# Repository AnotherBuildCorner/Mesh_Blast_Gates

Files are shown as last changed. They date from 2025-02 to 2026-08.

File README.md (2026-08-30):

# Mesh_Blast_Gates
## Currently Under Construction

What happens when you combine a Woodworker, and an Electrical Engineer? 
Sometimes the result are things like this. A Mesh controlled set of blast gates for dust collection control.

But first, why did I even bother making this? Cost, and Convenience. Products that can do this already exist on the market. However they cost somewhere around $125 USD PER GATE! Plus additional modules to handle higher power collection 230V systems. Plus I wanted to add advanced features like timers, and a rechargable pocket remote.

On top of that, I already had a fully built system utilizing manually actuated metal blast gates. It really felt like a total waste to rip these gates out in place of some closed solution. And some of the places i wanted to move my existing gates to are inacessible in the course of day to day operation. The commercial option has a switch mounted to the body. Which would impede that solution.

Instead I chose to launch my own system using my pre-existing knowledge of ESP32's and high power hobby servos. 

## Core Architecture.
First things first, the main parts:

The brains of the whole operation. Xiao C6 model ESP 32's. Chosen for their small form factor, while supporing enough GPIO pins to control the system, and supporting a socket mount (A wonderful bit of foresight... More on that later).

Additionally, I wanted a prebuilt serial system for flashing and monitoring, which this provides like many other DEV style boards.

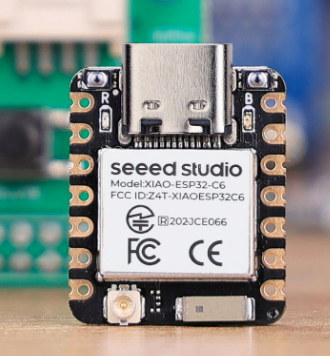
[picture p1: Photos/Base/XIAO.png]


The mechanics driving the actual gates are these servos: 20KG 270 deg servos, Relatively low cost, and when provided enough current/voltage have plenty of torque to do the job.

At right is the actual blast gate for reference.

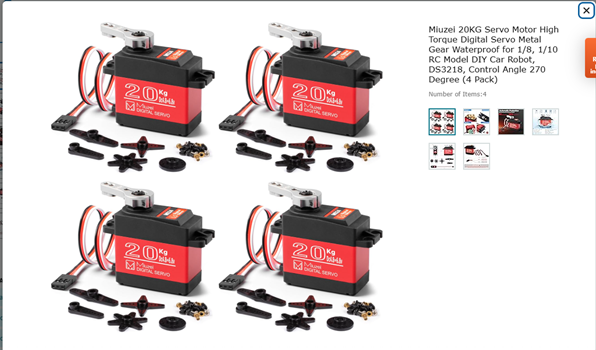
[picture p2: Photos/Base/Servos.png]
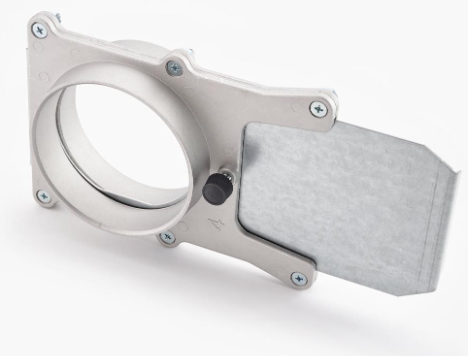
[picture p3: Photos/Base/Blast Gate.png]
  

Interconnect Diagram

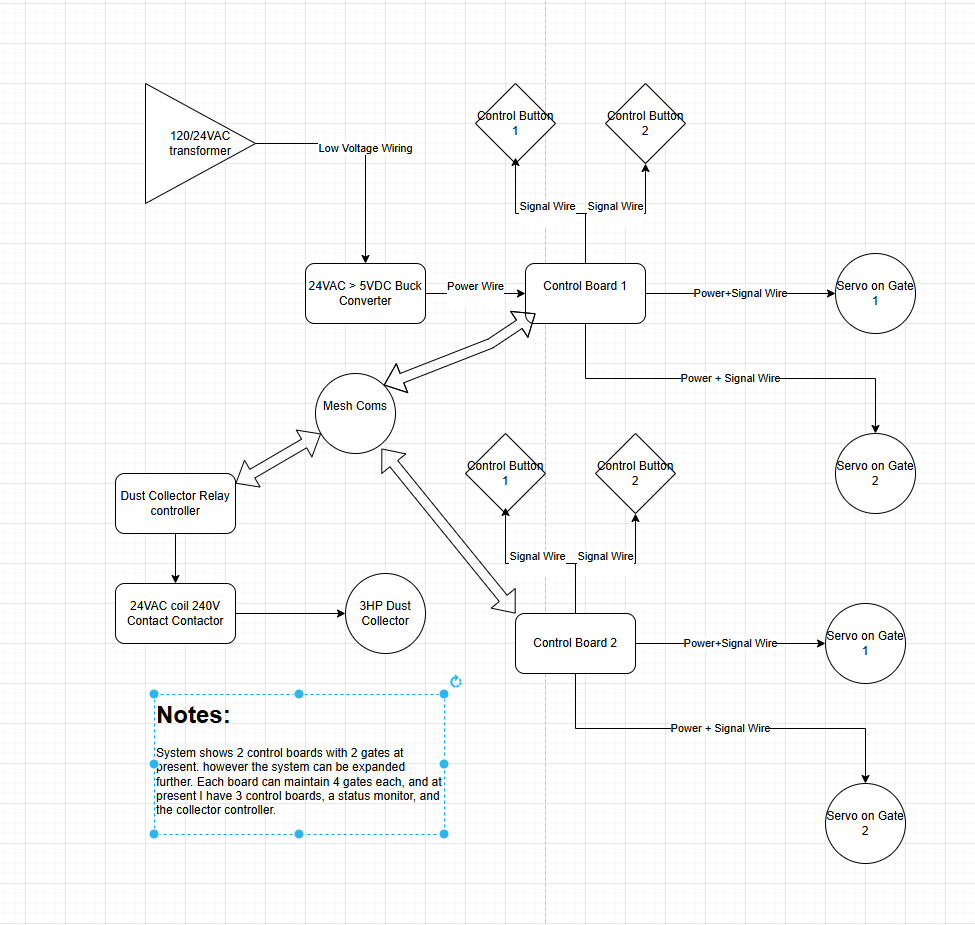
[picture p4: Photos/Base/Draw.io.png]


A rough picture of the pricing
Per Gate
- $20 per metal gate (already had on hand)
- $10 per servo
- $2 for 100G of 3D print Filament
- $2 misc overhead

Per Control Board as of Febuary 2025
- $5 per XIAO C6
- $1 per PCB
- $1 per Buck Boost Chip
- 1$ per Inductor (I used way oversized ones for low frequency switching)
- $5 rough estimate of additional parts (switches and such)
- $10 per USB power brick and cable (Some of us have mountains of these around) 

Per System cost
- $20 per 24V Transformer
- $10 per 204V-24V contactor
- $2 per 5V signal relay (for the collector control board)
- $5 per Xiao C6 for Collector only
- $20 for a roll of 22 gauge silicon wire for switches

So for my system, which uses 8 gates, 3 control boards, and a relay board the total cost comes up to around...
- Per gate costs: $ 280
- Per Board costs $ 69
- Per System costs $ 57
- Total: $ 416
- for my own cost I already had the blast gates and usb cables on hand, so -$ 190

## Notes:
There are some improvements left to be implemented. The core of which is still better power distribution/control. As well as updating the physical gate structures.
things i'd like to add
### PCB
- Completed desired updates. see V3
### Mechanical

- Add some form of mechanical clutch system.
- - Spring or screw compressed V band on the pinion (spring prefered, but introduces complexity and potential calibrations)
- - Switch from rack and pinion to V wheel and slider with TPU surface
- - add a slider into the rack with a helical spring mounted for bi-directional movement
- - Add TPU teeth to the rack or pinion so they can slip under excessive tension

### Code
- Current code has a strict 1HR timer on dust collection before shutdown
- modify to enable longer run times, or change the switch type specifically for the CNC to enable CNC controlled collection.
- maybe add a custom sender board just for the CNC. Not sure I want hard wires to a tool on wheels... (besides power)
- implement multi-gate control from one switch for cases like multiple gates to one tool
- add a multiple tool mode. Say having the CNC active and a drum sander. 
- consider changing the direct peer-peer mesh to a central node structure. Every time I have to replace one chip, reflashing the entire network is required... and some of the chips are hard to reach. Ideally an auto-detect model would be great.

## V3 

### PCB
V3 PCB is now live. Implementing two desired changes over the V2 Board.
The first is integrating the TVS diodes into the PCB on both the Servo signal lines, as well as the input switches. So far this has prevented any fried servos or bad ESP's in testing.
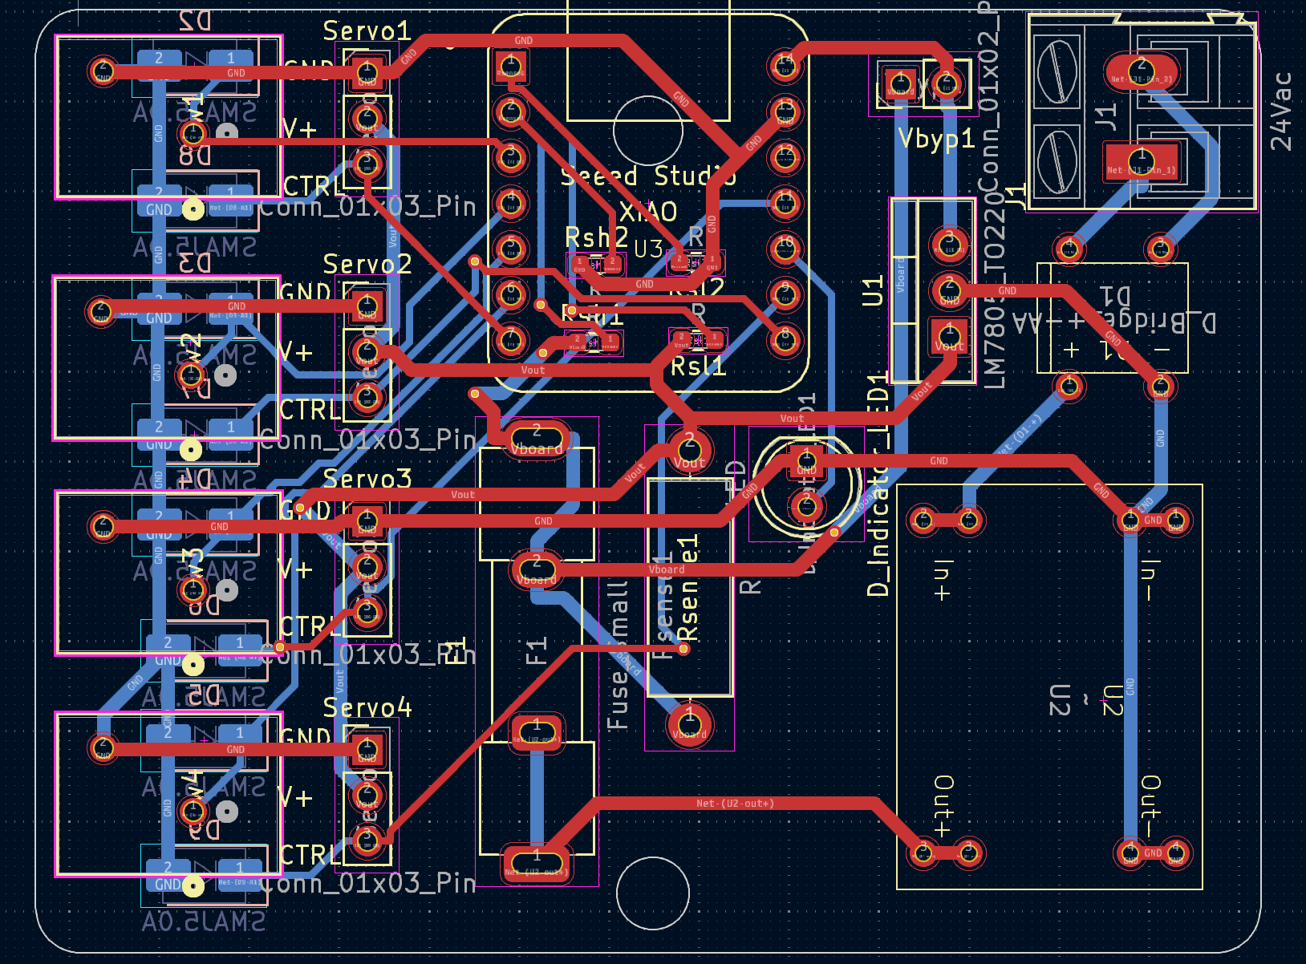
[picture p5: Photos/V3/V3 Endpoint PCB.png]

Second is the Buck-Boost board has been swapped for a commercially available premade PCB. The board provides up to 24V input, and trim controlled output. The PCB also includes a new LED tied directly to the ESP, this LED is programmed to illuminate between 7 and 8V currently to allow calibrating the new board.
The input Bridge Rectifier has been retained, as well as the smoothing cap. This allows for polarity agnotsic DC, as well as AC input for the boards. Currently running on 12V mains.

### Mechanical.
The gear drive system has been slightly refined.
The teeth are now 2mm straight cut gears, with a wider dual guide Rack, and a slot cut into one end to capture the blast gate without additional hardware. The baseplate has been thickened by an additional 2mm. and the gears now feature a multiple cut design on the underside to accomodate multiple servo horn shapes besides the round one. No more skipping of the gears now.
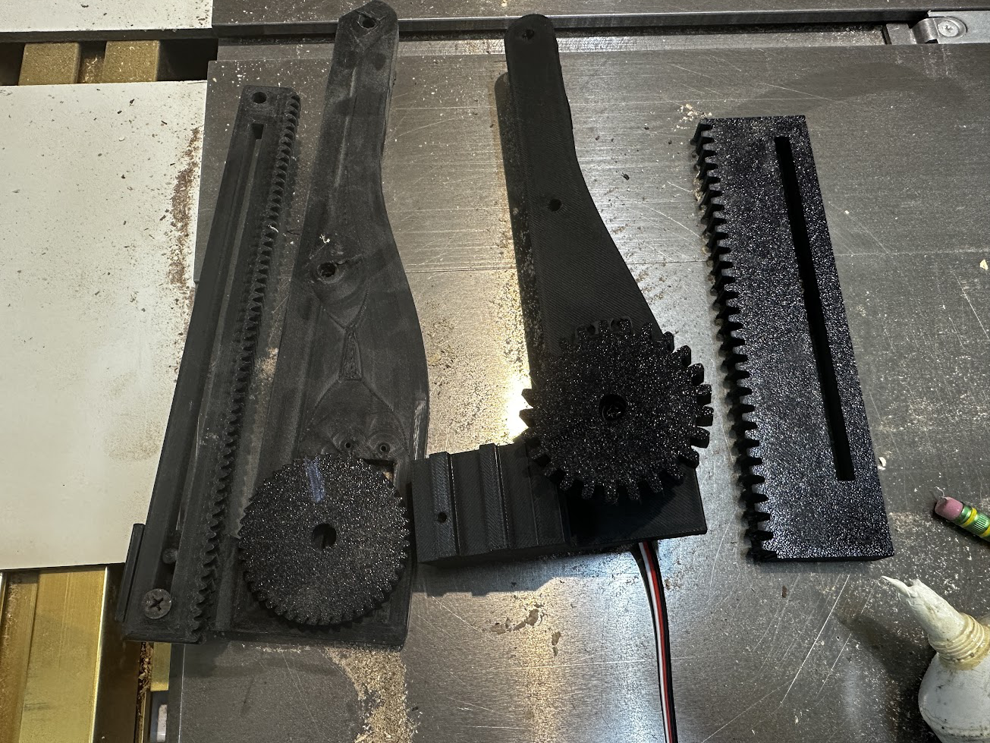
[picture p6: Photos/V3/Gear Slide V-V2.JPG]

### Code
The system now runs on a central node with a display screen. This way anytime the system is updated (say an ESP dies, or a new board is added) only the new board, and the central node need to be reflashed. Instead of correcting the entire system.
a strict 2 hour timer has been implemented for both short and long press gate openings.

Current sensing is back online in dual ended mode. With a 1.5A current limit, which enforces a chip reset currently. Future updates will force the gate to stop in position. No boards fried yet, but a couple fuses tripped due to user error.

Additionally, the central node has a configurable resend timer. In the past messages were failing to shut down the dust collector as required. With this resend, reliability has reached 100%, although sometimes it can take up to 3 cycles.

Future additions will be to include some kind of current sensing, or non-pushbutton operation perhaps. For things like CNC's with vacuum switching relays, or hall-effect sensors on certain tools. 
Also, the dual gate mode may be updated to set both gates to partially open, to retain system pressure.  TBD.
Lastly, it would be ideal to push all the configuration settings from the central node. so only a preliminary flash will be needed for each endpoint.  For now this is a stretch goal.

### Previous IN PROGRESS notes for V3
Well, as one set of errors is removed, a new set begins to rear its ugly head. 

### PCB
At present a new PCB has not been generated. Currently in the troubleshooting phase.
As it stands right now, it appears the system would function on a metal ducted dust collection system, because the entire tubing would have an ESD potential of 0, being grounded somewhere. However, my system is PVC based, as such it collects static charges.

Initially I did not pursue ESD hardening because I did my best to isolate the switch wires from the dust pipe runs, as well as the servos are on isolated plastic brackets, again with minimum wire near the potentially charged pipes.

However this has not been enough. As it seems the ESP32 chips have been bricking at seemingly random times. Although it always seems to be on a chip that had an active flow of air through a connected gate, which was then switched to a different gate. 

To rectify this, I have placed Unidirectional TVS diodes in two places thus far. The first batch went on each of the input switches connected from signal to ground. This alone did not fix the problem, as shortly after implementing, another board fried.
The second batch is connected from each of the servo signal wires to ground. This setup remains to be tested.

Board with TVS Diodes added: Note, the switches are configured in switch to ground with PULL_UP enabled on the XIAO. So the TVS diodes clamp the voltage to 5V which is within acceptable ranges for the XIAO even though it's a 3.3V microcontroller.

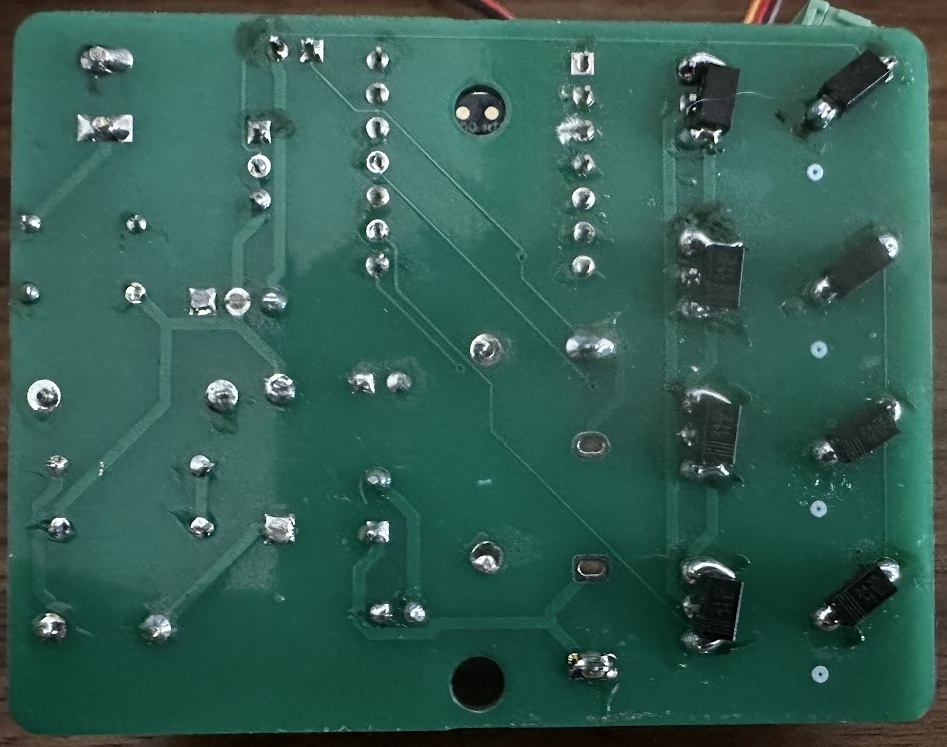
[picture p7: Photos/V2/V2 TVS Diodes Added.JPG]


For now I have switched to powering the system on 5V 1A usb power supplies for each module, as I ran out of the Buck controller chips, and as of right now USB power has proven more than powerful enough to control all but my largest gate with the entire system closed and under vacuum. Additionally I encountered some bad wire that had internal insulation problems which shorted out my transformer.  Sometimes it's best to know when to stick with what's working...  I will likely revisit the Buck controller at a later date. First is solving the frying ESP32's  otherwise this system is a useless brick.

## V2
Version 2 corrects a lot of the mistakes Version 1 made, and has resulted in a functional system, but is still far from complete.

### PCBs 
First, the PCB has been updated to contain power limiting safety measures. Among these are Fuse 1, set to a 1 amp glass tube fuse. and the addition of the large curent sense resistor RSense. Additionally a network of voltage dividers has been added to drop the 5-7 volt voltages at Rsense terminals to the 3.3V the ESP ADC can handle.

The system uses dual ended current sensing, with the resistance of Rsense known to within 1% and programmed. Voltage is measured at each terminal, the difference calculated, and from that current through the resistor is determined. This is used to initiate a restart in the code. As the gates are programmed to not move until a command is sent, this functions as a pause. This is temporary, in time a better response to a binding gate, like bounce or a simple stop will be implemented.

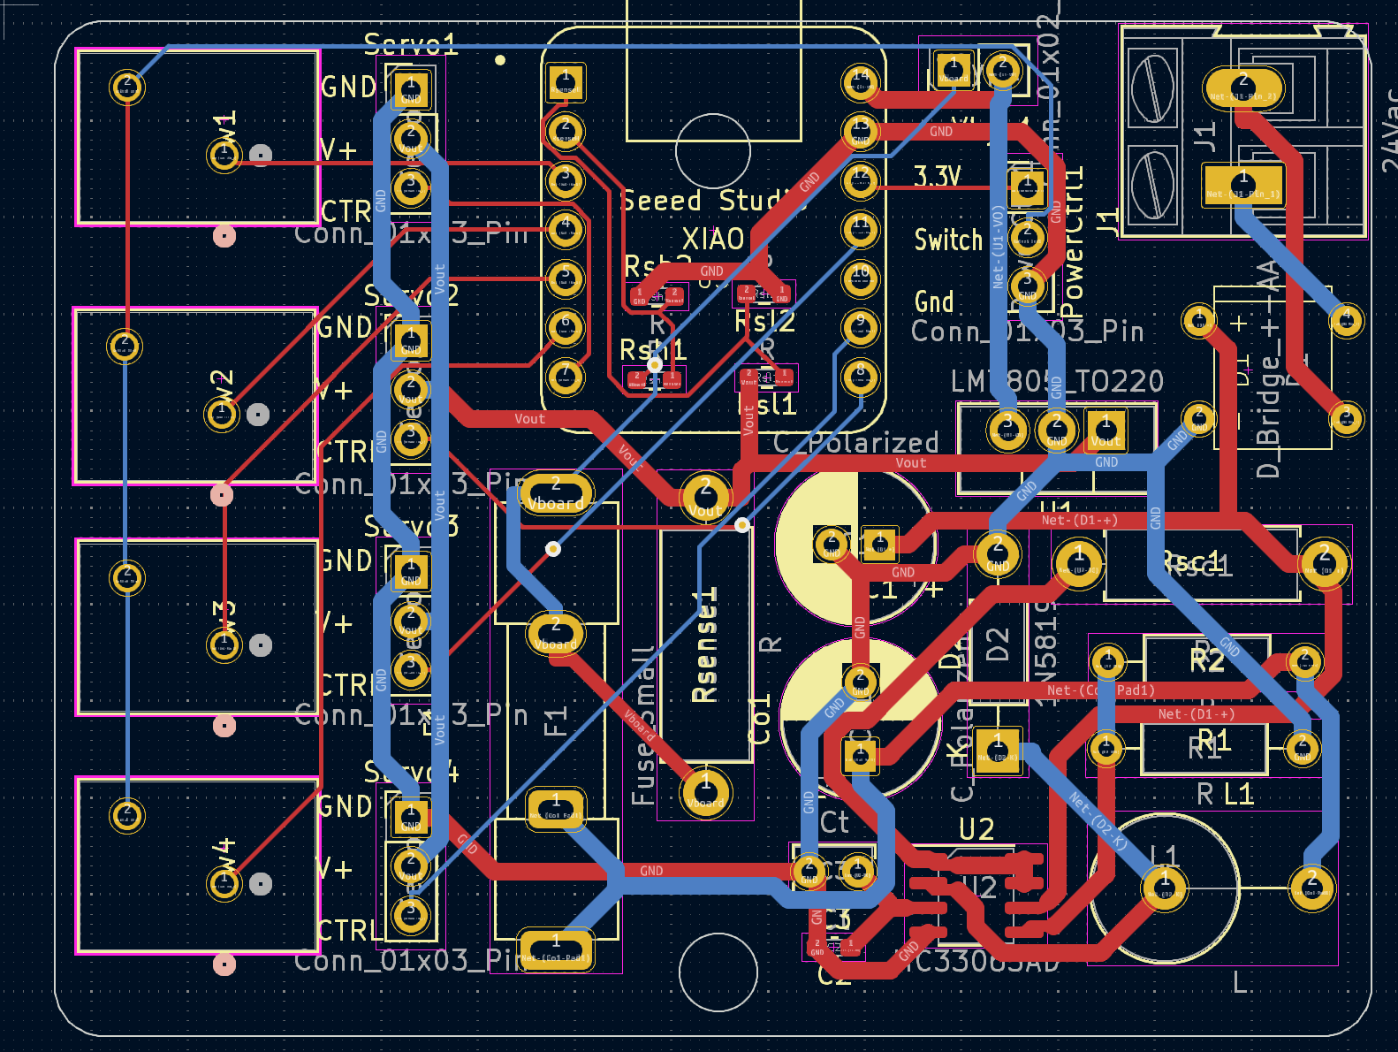
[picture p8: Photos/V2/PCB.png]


Additionally, a second PCB for controlling two possible Dust collection units has been added.

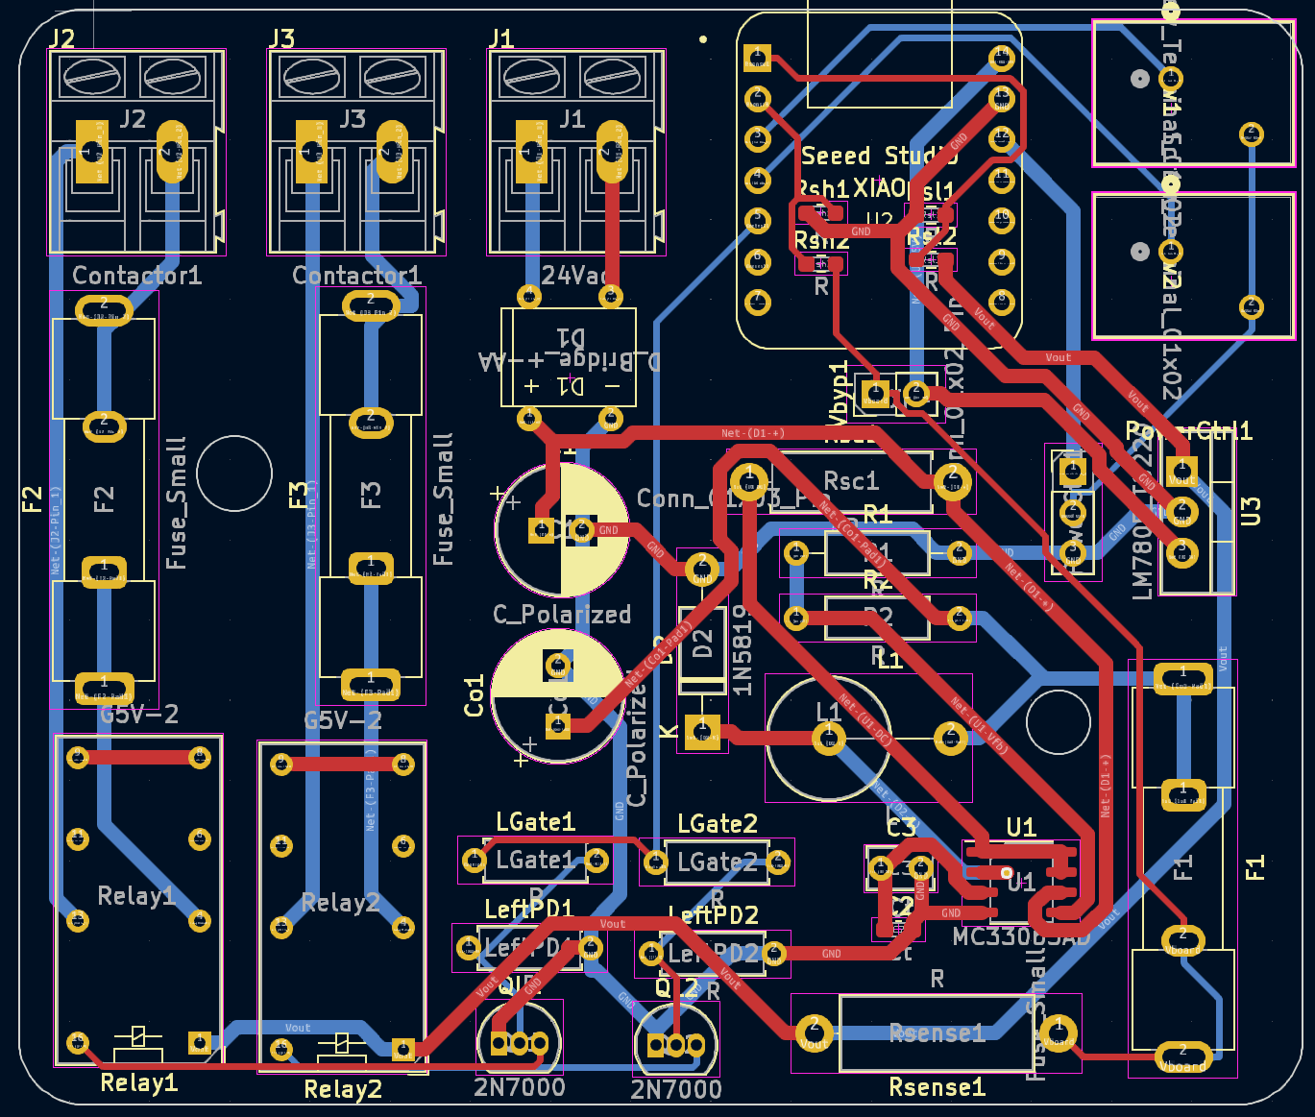
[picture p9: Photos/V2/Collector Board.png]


### Mechanical

On the mechanical aspect, the piston arrangement has been replaced with a rack and pinion. 
Advantages
- More positive mechanical engagement
- less servo torque required for actuation
- uses more of the available 270deg servo throw

Disadvantages
- takes up more space due to the rack
- also requires more material to 3D print increasing overall cost
- the gears can sometimes skip (this is more a poor implementation than a flaw of the rack itself)
- without precise limits in the code, binding, or semi-open gates are a problem. Yet somehow for identical parts, the limits are sightly different for each gate.

More precisely, a Herringbone rack and pinion was 3D printed.The herringbone is specifically for it's self aligning aspect, so the rack is unlikely to slip off the pinion without being captured somehow.

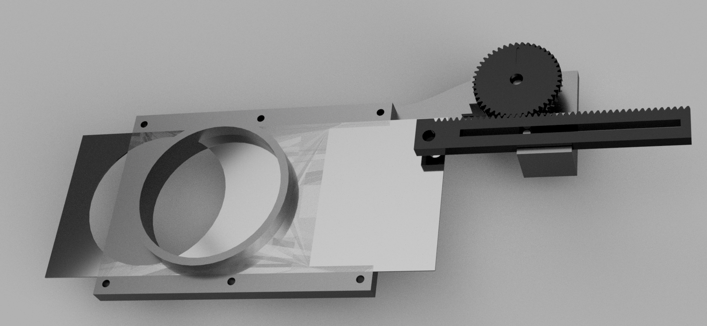
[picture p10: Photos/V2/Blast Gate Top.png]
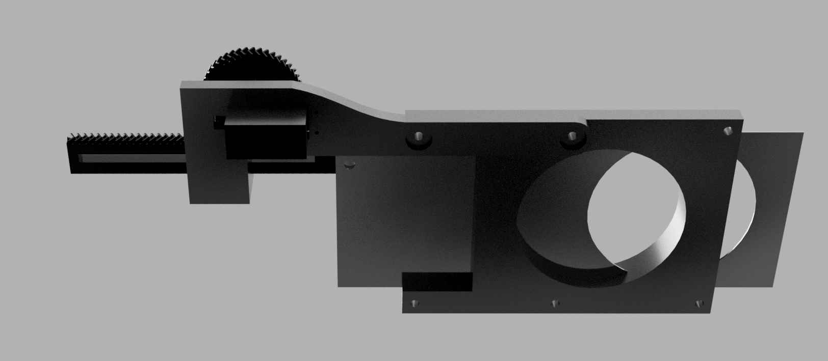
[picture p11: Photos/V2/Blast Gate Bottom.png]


[Rack and Pinion in operation.mov](<Photos/V2/Gate Operation.MOV>)

## V1
It's safe to consider this a very flawed early prototype. A lot of mistakes were made.
Primarily you will note the absence of any sort of fuses/safety devices. This will really come back to bite later.

The problem is the system is a semi-closed loop design. I say that because internally each servo is closed loop, It knows its position, and the desired target position. However this position does not make it back to the contol board. So to the controller, the system is open loop.

Why is this a problem? Because each control board is fed a set of target limits for open and close. And the servo will either reach that position, or push until it's internal overload trips. Problem is the servo can pull upwards of 5A at 7V in "stall" operation. which is way more than the Buck controller is rated for.

Now under normal circumstances this isn't an issue, as the programming has delays designed to slow the servo's operation, lowering the current output. However, on startup sometimes the gates are in the wrong place, as power off location memory has not been implemented yet, and attempt to return home rapidly. Or the limits get slightly out of whack, and the servo stalls. When supplied by USB power, this isn't an issue, as the XIAO's internal brownout detector triggers. But with this external supply that limiter doesn't exist. So instead, fried Buck chips, and not the edible kind either.

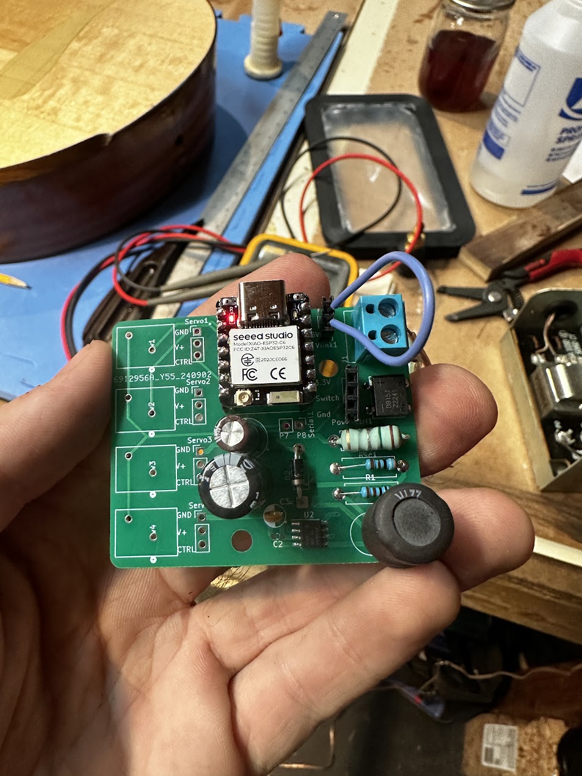
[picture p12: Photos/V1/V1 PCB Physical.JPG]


### Mechanical

The problems above were exacerbated by a poor choice of mechanical arrangement. The first iteration used a piston like arrangement. Which in practice was great on opening. But tended to bind horribly on close, stalling the servo, and yes, you guessed it, fried chips.

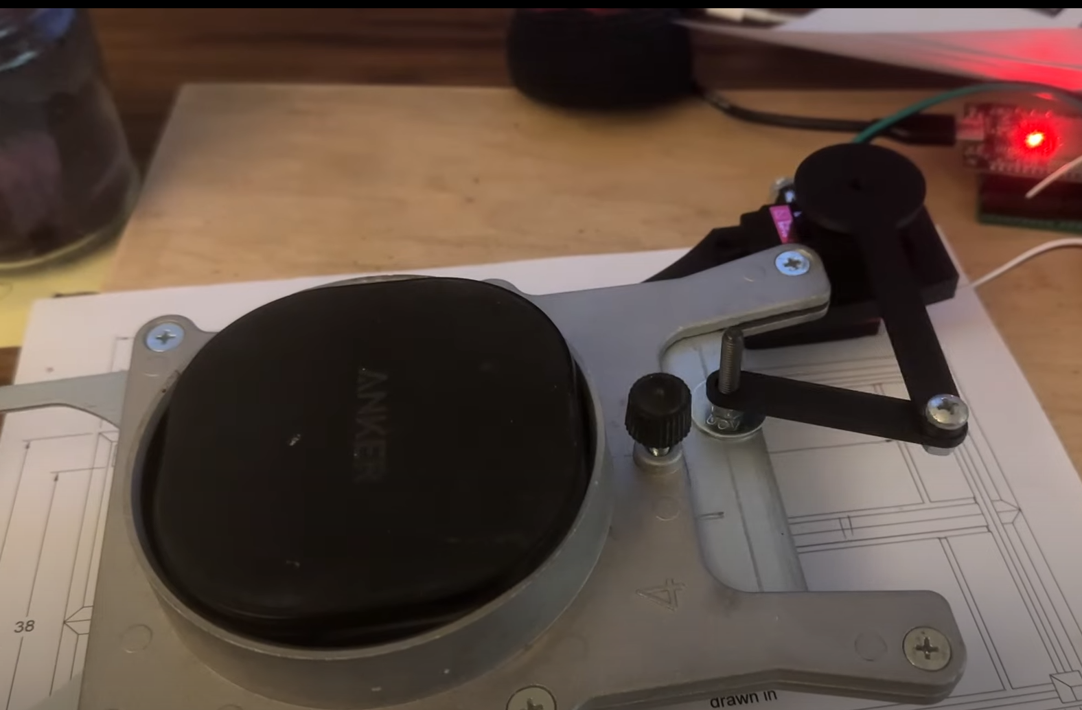
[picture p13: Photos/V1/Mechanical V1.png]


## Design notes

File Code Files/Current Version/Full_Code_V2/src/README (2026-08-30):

Last notes. Attempted to add 

if(GateStatusLongPress[i] == true && BoardData.collectorstate == false){
  boarddata.collectorstate == true
}

To catch the rare time when the timers shut down the collector, while leaving the blast gates open. however it appears the control scheme for the collector being defined as any one gate being open is overriding this and forcing the gate to toggle anyways.
Ignoring for the moment, will find out if the timers even cause problems in practice, as in principle they are only a safety measure.

Also, turning the system off when a long press gate is open might be tedious. 
At present the called for method is either long pressing the correct gate, or long then short pressing any gate, or short then long, either way this trips the gate overlap function which reverts to the short press being considered "open"  

Perhaps a double tap to toggle dust collector option is required. which may require redefining the way the central node determines if the collector is active.

Current sensing remains disabled for the moment.

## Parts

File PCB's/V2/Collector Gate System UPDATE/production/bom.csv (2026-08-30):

Designator | Footprint | Quantity | Value | LCSC Part #
D1 | DB_M | 1 | D_Bridge_+-AA
D2, D3, D4, D5, D6, D7, D8, D9 | D_SMA | 8 | SMAJ5.0A
D_INDICATOR_LED1 | LED_D5.0mm_Clear | 1 | LED
F1 | Fuseholder_Clip-5x20mm_Keystone_3512P_Inline_P23.62x7.27mm_D1.02x2.41x1.02x1.57mm_Horizontal | 1 | Fuse_Small
J1 | TerminalBlock_Altech_AK300-2_P5.00mm | 1 | 24Vac
RSENSE1 | R_Axial_DIN0414_L11.9mm_D4.5mm_P15.24mm_Horizontal | 1 | R
RSH1, RSH2, RSL1, RSL2 | 0603 | 4 | R
SERVO1, SERVO2, SERVO3, SERVO4 | PinHeader_1x03_P2.54mm_Vertical | 4 | Conn_01x03_Pin
SW1, SW2, SW3, SW4 | CONN_1985195 | 4 | Screw_Terminal_01x02
U1 | TO-220-3_Vertical | 1 | LM7805_TO220
U2 | MS1584_fullboard | 1 | ~
U3 | XIAO-Generic-Thruhole-14P-2.54-21X17.8MM | 1 | ~
VBYP1 | PinHeader_1x02_P2.54mm_Vertical | 1 | Conn_01x02_Pin

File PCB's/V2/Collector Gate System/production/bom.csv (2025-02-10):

Designator | Footprint | Quantity | Value | LCSC Part #
C1 | CP_Radial_D8.0mm_P2.50mm | 1 | C_Polarized
C2 | 0603 | 1 | Ct
C3 | C_Rect_L4.0mm_W2.5mm_P2.50mm | 1 | Ct
Co1 | CP_Radial_D8.0mm_P3.80mm | 1 | C_Polarized
D1 | DB_M | 1 | D_Bridge_+-AA
D2 | D_DO-41_SOD81_P10.16mm_Horizontal | 1 | 1N5819
F1 | Fuseholder_Clip-5x20mm_Keystone_3512P_Inline_P23.62x7.27mm_D1.02x2.41x1.02x1.57mm_Horizontal | 1 | Fuse_Small
J1 | TerminalBlock_Altech_AK300-2_P5.00mm | 1 | 24Vac
L1 | L_Axial_L16.0mm_D7.5mm_P7.62mm_Vertical_Fastron_XHBCC | 1 | L
PowerCtrl1, Servo1, Servo2, Servo3, Servo4 | PinHeader_1x03_P2.54mm_Vertical | 5 | Conn_01x03_Pin
R1, R2 | R_Axial_DIN0207_L6.3mm_D2.5mm_P10.16mm_Horizontal | 2 | R
Rsc1 | R_Axial_DIN0411_L9.9mm_D3.6mm_P12.70mm_Horizontal | 1 | R
Rsense1 | R_Axial_DIN0414_L11.9mm_D4.5mm_P15.24mm_Horizontal | 1 | R
Rsh1, Rsh2, Rsl1, Rsl2 | 0603 | 4 | R
Sw1, Sw2, Sw3, Sw4 | CONN_1985195 | 4 | Screw_Terminal_01x02
U1 | TO-220-3_Vertical | 1 | LM7805_TO220
U2 | SOIC-8_3.9x4.9mm_P1.27mm | 1 | MC33063AD
U3 | XIAO-Generic-Thruhole-14P-2.54-21X17.8MM | 1 | ~
Vbyp1 | PinHeader_1x02_P2.54mm_Vertical | 1 | Conn_01x02_Pin

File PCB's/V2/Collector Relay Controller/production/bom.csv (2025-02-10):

Designator | Footprint | Quantity | Value | LCSC Part #
C1 | CP_Radial_D8.0mm_P2.50mm | 1 | C_Polarized
C2 | 0603 | 1 | Ct
C3 | C_Rect_L4.0mm_W2.5mm_P2.50mm | 1 | Ct
Co1 | CP_Radial_D8.0mm_P3.80mm | 1 | C_Polarized
D1 | DB_M | 1 | D_Bridge_+-AA
D2 | D_DO-41_SOD81_P10.16mm_Horizontal | 1 | 1N5819
F1, F2, F3 | Fuseholder_Clip-5x20mm_Keystone_3512P_Inline_P23.62x7.27mm_D1.02x2.41x1.02x1.57mm_Horizontal | 3 | Fuse_Small
J1 | TerminalBlock_Altech_AK300-2_P5.00mm | 1 | 24Vac
J2, J3 | TerminalBlock_Altech_AK300-2_P5.00mm | 2 | Contactor1
L1 | L_Axial_L16.0mm_D7.5mm_P7.62mm_Vertical_Fastron_XHBCC | 1 | L
LGate1, LGate2, LeftPD1, LeftPD2 | R_Axial_DIN0207_L6.3mm_D2.5mm_P7.62mm_Horizontal | 4 | R
PowerCtrl1 | PinHeader_1x03_P2.54mm_Vertical | 1 | Conn_01x03_Pin
QL1, QL2 | TO-92_Inline | 2 | 2N7000
R1, R2 | R_Axial_DIN0207_L6.3mm_D2.5mm_P10.16mm_Horizontal | 2 | R
Relay1, Relay2 | Relay_DPDT_Omron_G5V-2 | 2 | G5V-2
Rsc1 | R_Axial_DIN0411_L9.9mm_D3.6mm_P12.70mm_Horizontal | 1 | R
Rsense1 | R_Axial_DIN0414_L11.9mm_D4.5mm_P15.24mm_Horizontal | 1 | R
Rsh1, Rsh2, Rsl1, Rsl2 | 0603 | 4 | R
Sw1, Sw2 | CONN_1985195 | 2 | Screw_Terminal_01x02
U1 | SOIC-8_3.9x4.9mm_P1.27mm | 1 | MC33063AD
U2 | XIAO-Generic-Thruhole-14P-2.54-21X17.8MM | 1 | ~
U3 | TO-220-3_Vertical | 1 | LM7805_TO220
Vbyp1 | PinHeader_1x02_P2.54mm_Vertical | 1 | Conn_01x02_Pin

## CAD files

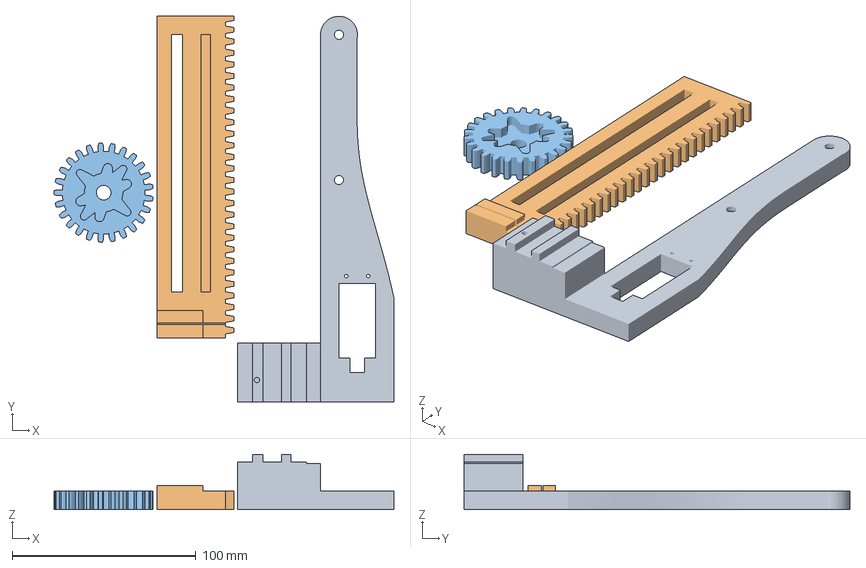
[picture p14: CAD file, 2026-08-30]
Mechanical/V3/4 inch servo gate geared v11.3mf
184.9 x 209.6 x 30.0 mm

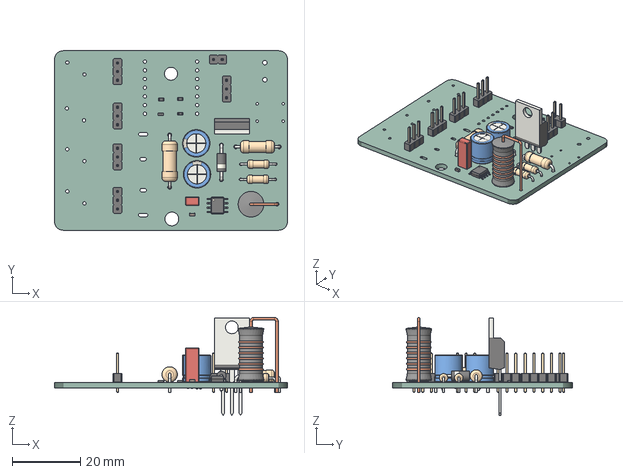
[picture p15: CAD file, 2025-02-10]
PCB's/V2/Collector Gate System UPDATE/Collector Gate System.step
68.1 x 52.5 x 28.6 mm
Collector Gate System PCB

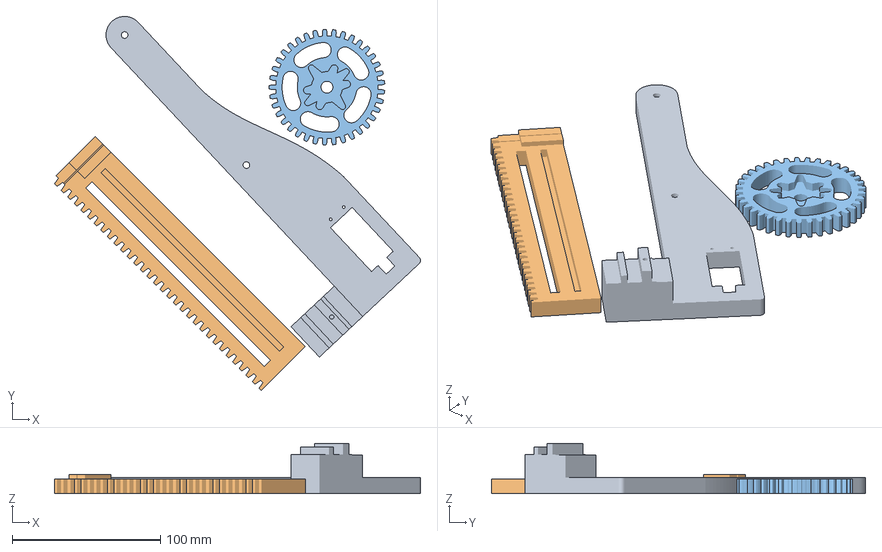
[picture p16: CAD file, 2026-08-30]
Mechanical/V3/6 Inch servo gate v3.3mf
246.5 x 252.0 x 34.0 mm

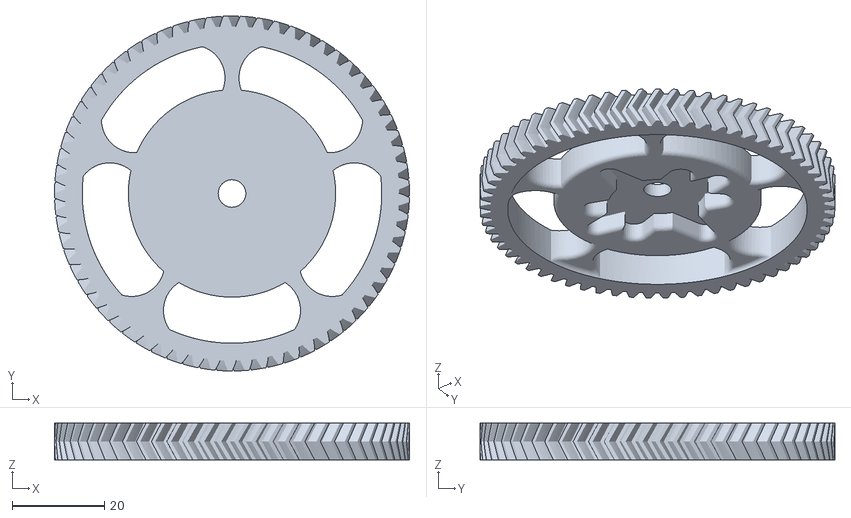
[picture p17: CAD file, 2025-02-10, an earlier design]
Mechanical/V2/6 inch gate pinion.stl
77.1 x 77.1 x 8.00

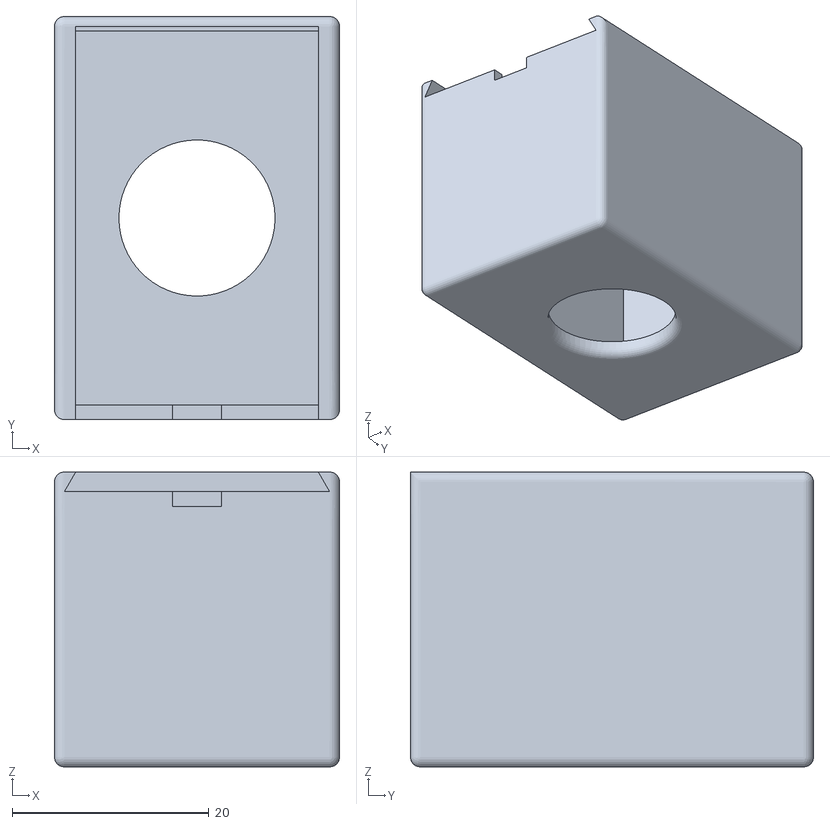
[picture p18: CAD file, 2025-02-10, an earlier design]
Mechanical/V2/Button Body.stl
29.0 x 41.0 x 30.0

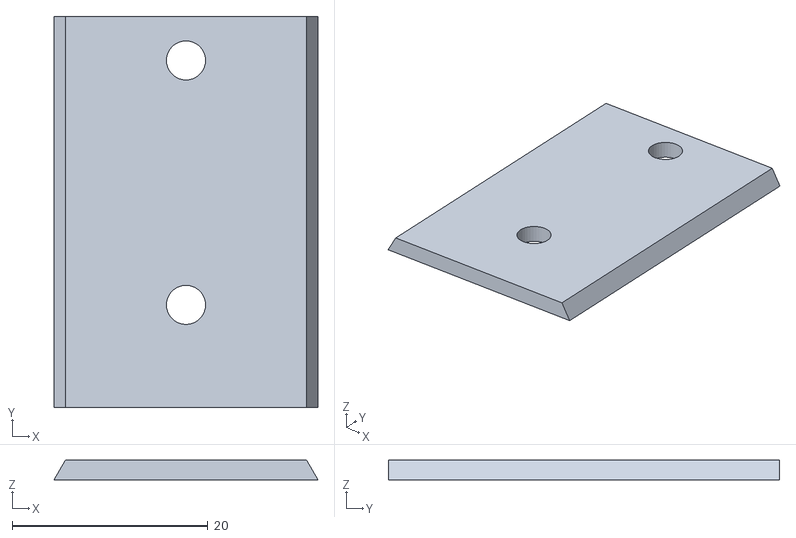
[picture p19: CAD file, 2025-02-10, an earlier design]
Mechanical/V2/Button Slide.stl
27.0 x 40.0 x 2.00

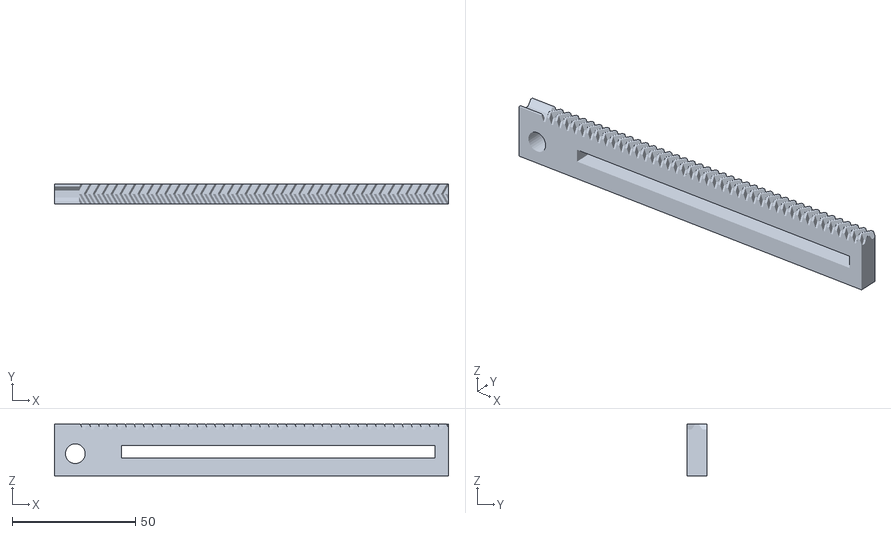
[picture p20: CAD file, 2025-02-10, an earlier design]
Mechanical/V2/Drive Rack.stl
160.0 x 8.00 x 21.0

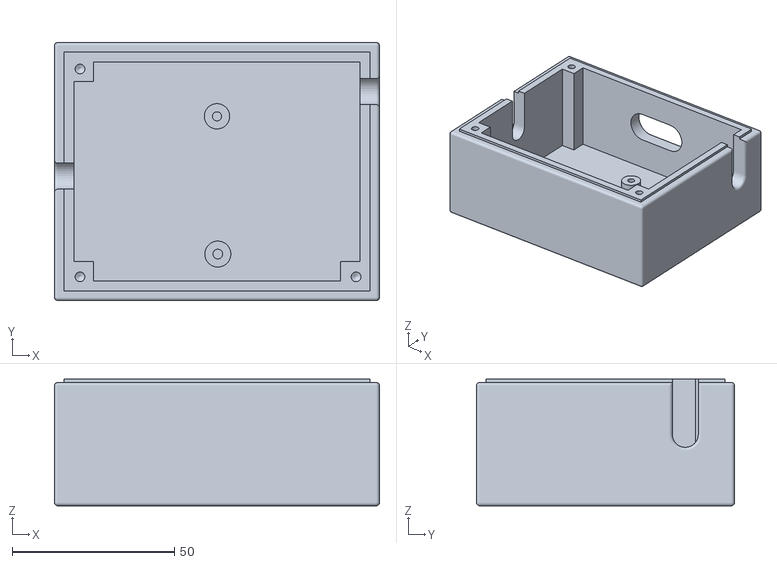
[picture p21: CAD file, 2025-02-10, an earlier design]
Mechanical/V2/V2 Control Box.stl
100.1 x 79.5 x 39.0

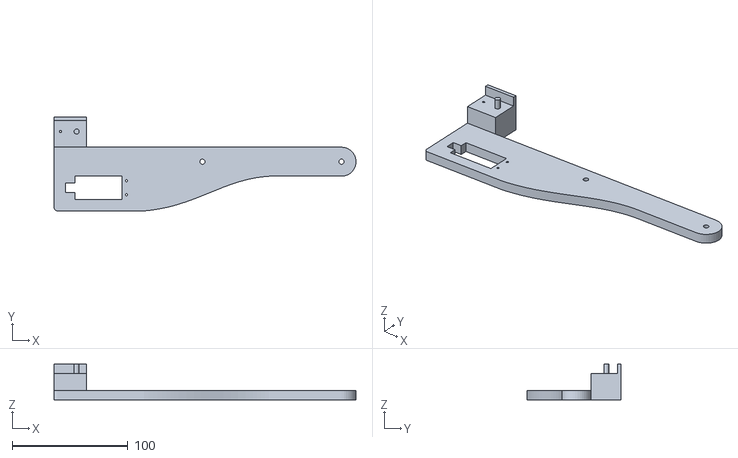
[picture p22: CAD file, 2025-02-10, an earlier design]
Mechanical/V2/6 inch gate servo holder.stl
260.5 x 81.0 x 31.0

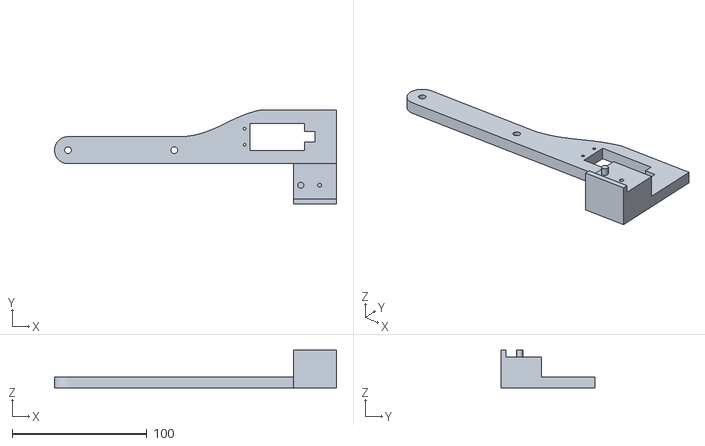
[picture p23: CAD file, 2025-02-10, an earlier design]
Mechanical/V2/Servo Holder.stl
209.6 x 70.0 x 28.0

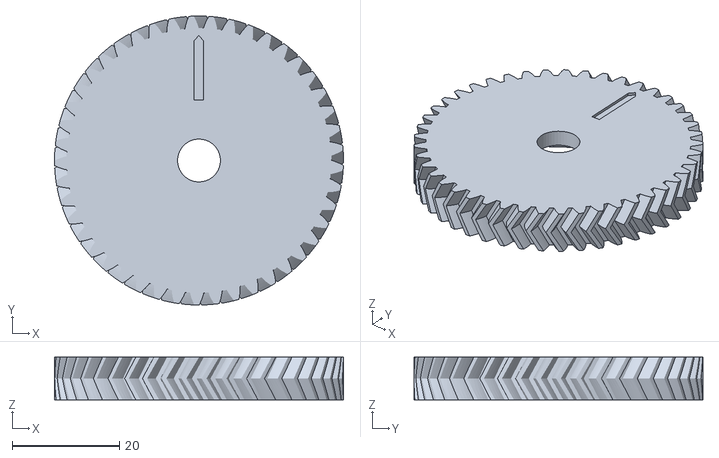
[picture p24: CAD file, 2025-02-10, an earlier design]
Mechanical/V2/Drive Gear V2.stl
54.0 x 54.0 x 8.00

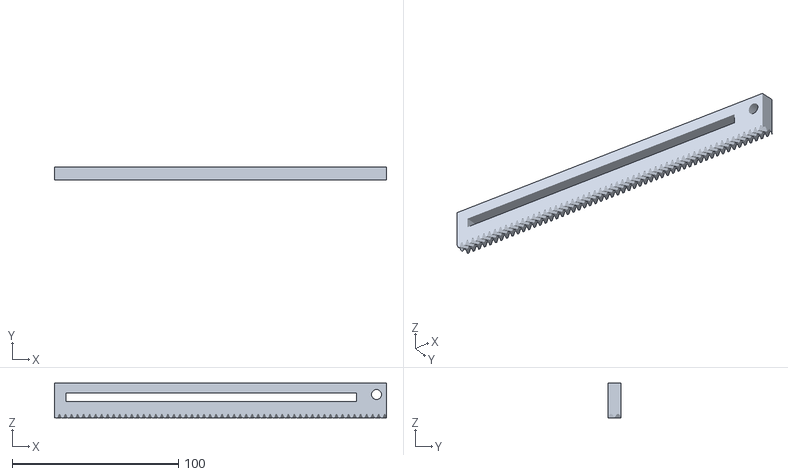
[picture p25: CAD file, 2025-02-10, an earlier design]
Mechanical/V2/6 inch gate rack.stl
200.0 x 8.00 x 21.0

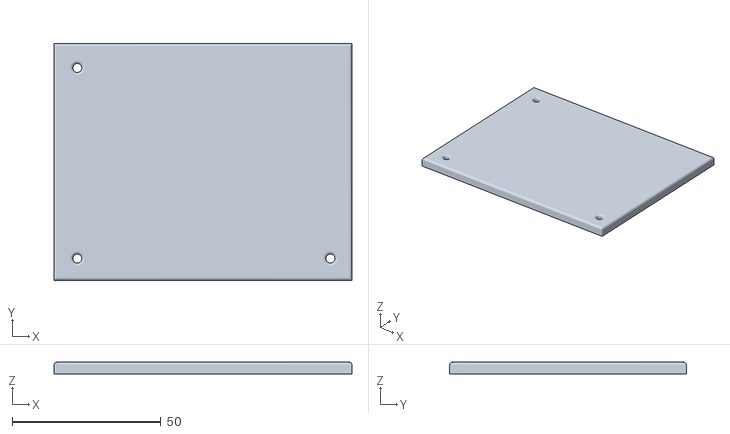
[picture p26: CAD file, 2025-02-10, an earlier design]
Mechanical/V2/V2 Control Lid.stl
100.1 x 79.5 x 4.00

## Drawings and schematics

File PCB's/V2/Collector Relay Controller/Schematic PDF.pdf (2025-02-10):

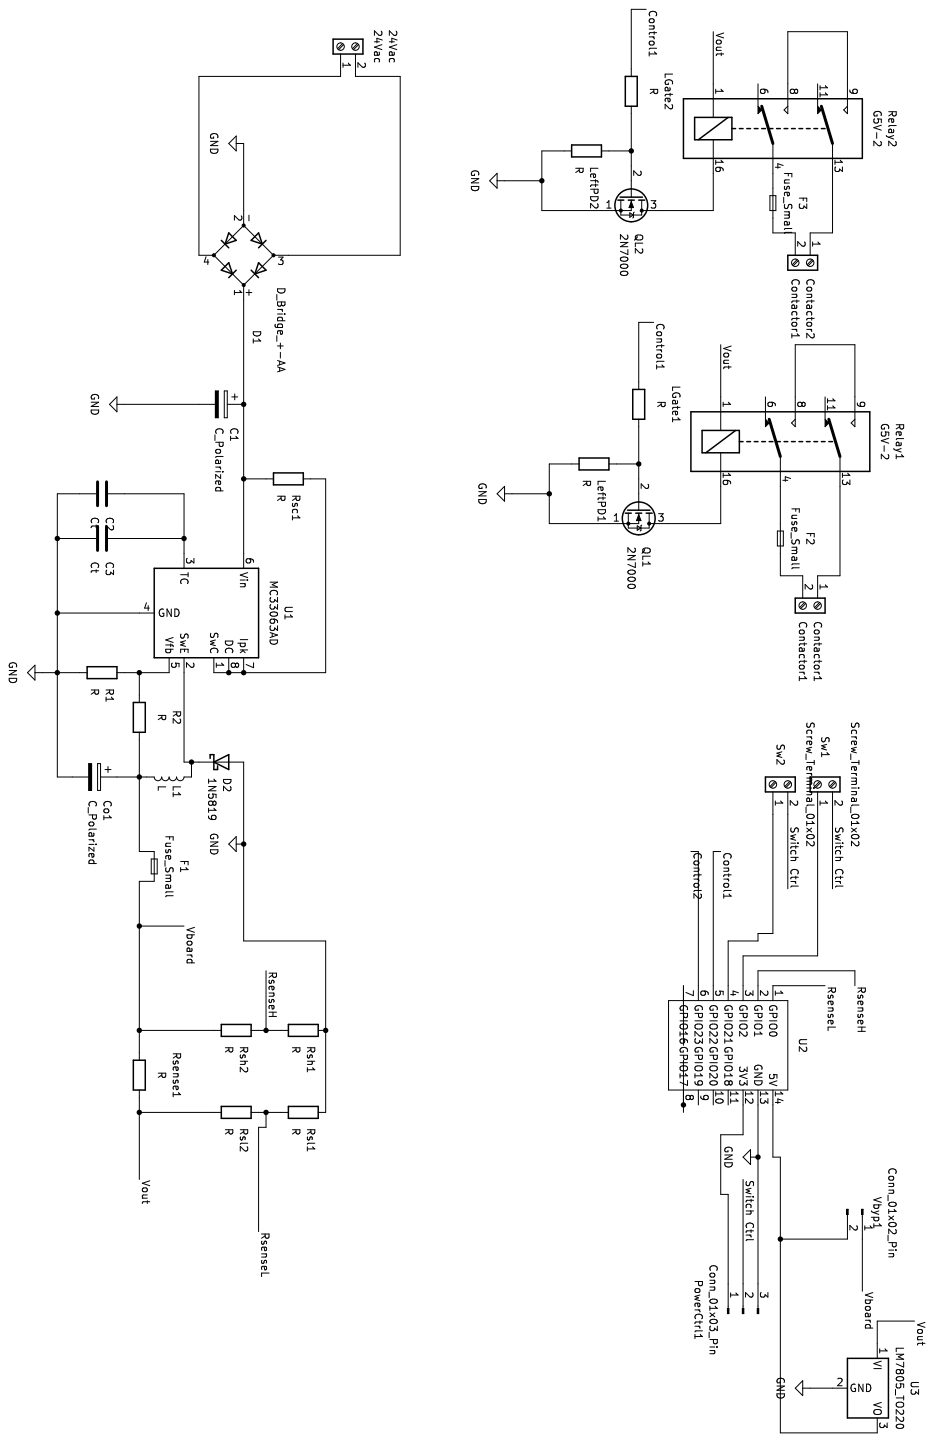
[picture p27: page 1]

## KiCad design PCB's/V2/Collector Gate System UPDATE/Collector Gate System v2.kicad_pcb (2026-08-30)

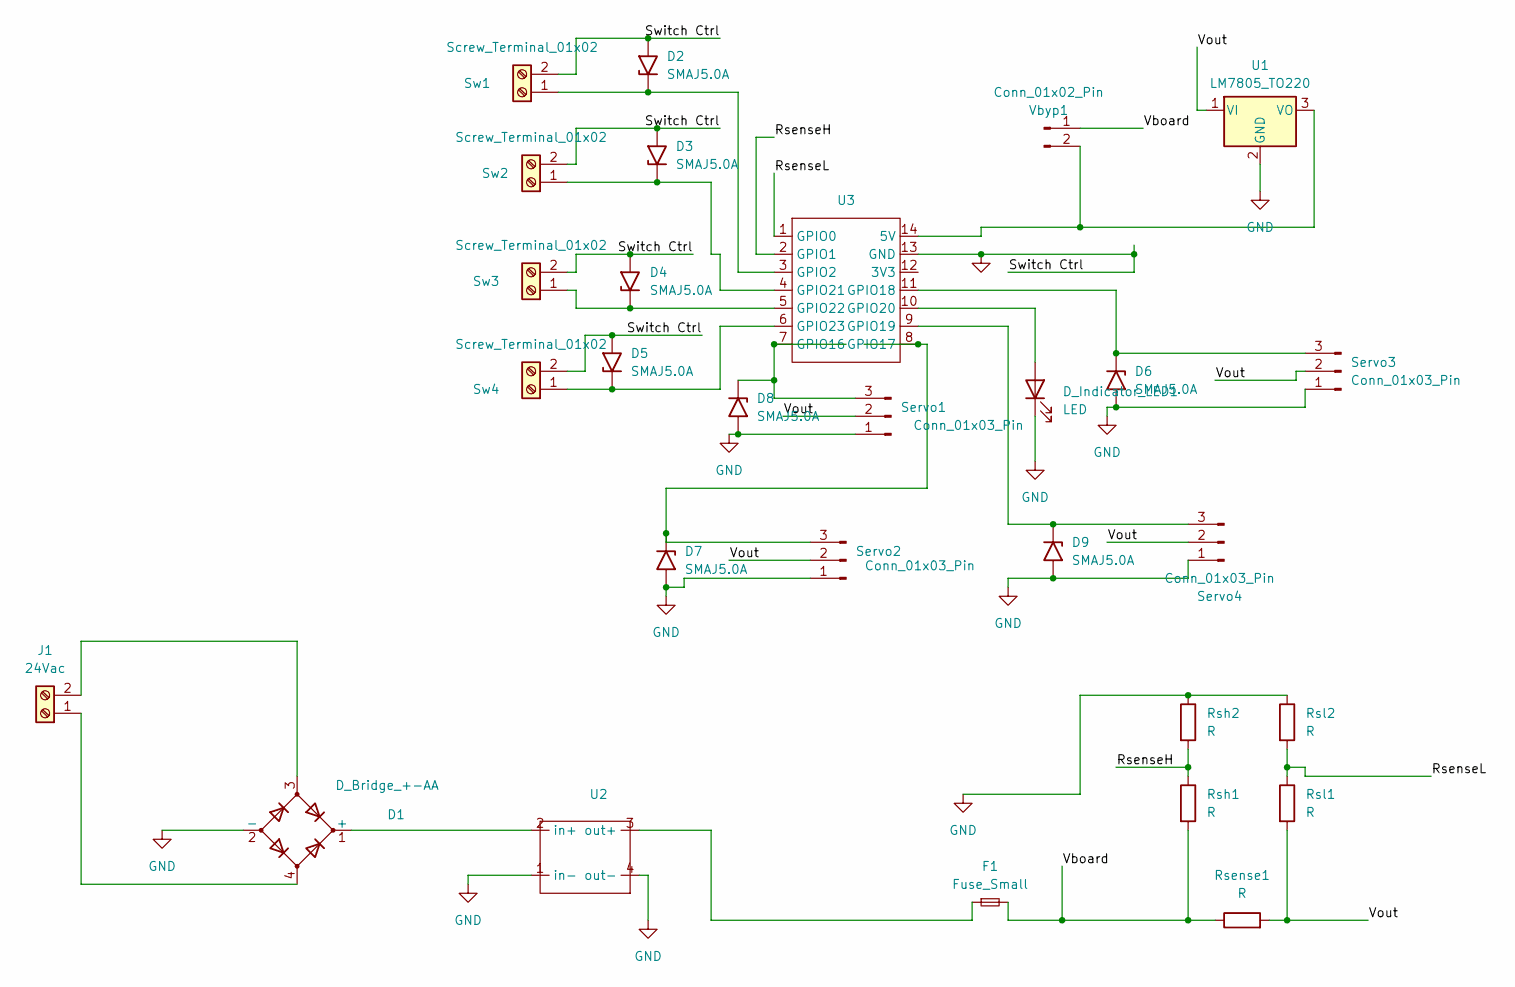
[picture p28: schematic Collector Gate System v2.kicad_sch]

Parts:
D1: D_Bridge_+-AA; DB_M
D2, D3, D4, D5, D6, D7, D8, D9: SMAJ5.0A; D_SMA
D_Indicator_LED1: LED; LED_D5.0mm_Clear
F1: Fuse_Small; Fuseholder_Clip-5x20mm_Keystone_3512P_Inline_P23.62x7.27mm_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
J1: 24Vac; TerminalBlock_Altech_AK300-2_P5.00mm
Rsense1: R; R_Axial_DIN0414_L11.9mm_D4.5mm_P15.24mm_Horizontal
Rsh1, Rsh2: R; R_0603_1608Metric_Pad0.98x0.95mm_HandSolder
Rsl1, Rsl2: R; R_0603_1608Metric_Pad0.98x0.95mm_HandSolder
Servo1, Servo2, Servo3, Servo4: Conn_01x03_Pin; PinHeader_1x03_P2.54mm_Vertical
Sw1, Sw2, Sw3, Sw4: Screw_Terminal_01x02; CONN_1985195
U1: LM7805_TO220; TO-220-3_Vertical
U2: MS1584_fullboard
U3: XIAO-Generic-Thruhole-14P-2.54-21X17.8MM
Vbyp1: Conn_01x02_Pin; PinHeader_1x02_P2.54mm_Vertical

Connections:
/RsenseH: Rsh1.1, Rsh2.2, U3.2 (GPIO1)
/RsenseL: Rsl1.1, Rsl2.2, U3.1 (GPIO0)
/Vboard: F1.2, Rsense1.1, Rsh1.2, Vbyp1.1
/Vout: Rsense1.2, Rsl1.2, Servo1.2, Servo2.2, Servo3.2, Servo4.2, U1.1 (VI)
GND: D1.2 (-), D2.2 (A2), D3.2 (A2), D4.2 (A2), D5.2 (A2), D6.2 (A2), D7.2 (A2), D8.2 (A2), D9.2 (A2), D_Indicator_LED1.1 (K), Rsh2.1, Rsl2.1, Servo1.1, Servo2.1, Servo3.1, Servo4.1, Sw1.2, Sw2.2, Sw3.2, Sw4.2, U1.2 (GND), U2.1 (in-), U2.4 (out-), U3.13 (GND)
unnamed: D1.1 (+), U2.2 (in+)
unnamed: D2.1 (A1), Sw1.1, U3.3 (GPIO2)
unnamed: D3.1 (A1), Sw2.1, U3.4 (GPIO21)
unnamed: D4.1 (A1), Sw3.1, U3.5 (GPIO22)
unnamed: D5.1 (A1), Sw4.1, U3.6 (GPIO23)
unnamed: D6.1 (A1), Servo3.3, U3.11 (GPIO18)
unnamed: D7.1 (A1), Servo2.3, U3.8 (GPIO17)
unnamed: D8.1 (A1), Servo1.3, U3.7 (GPIO16)
unnamed: D9.1 (A1), Servo4.3, U3.9 (GPIO19)
unnamed: D_Indicator_LED1.2 (A), U3.10 (GPIO20)
unnamed: D1.4, J1.1
unnamed: D1.3, J1.2
unnamed: U1.3 (VO), U3.14 (5V), Vbyp1.2
unnamed: F1.1, U2.3 (out+)

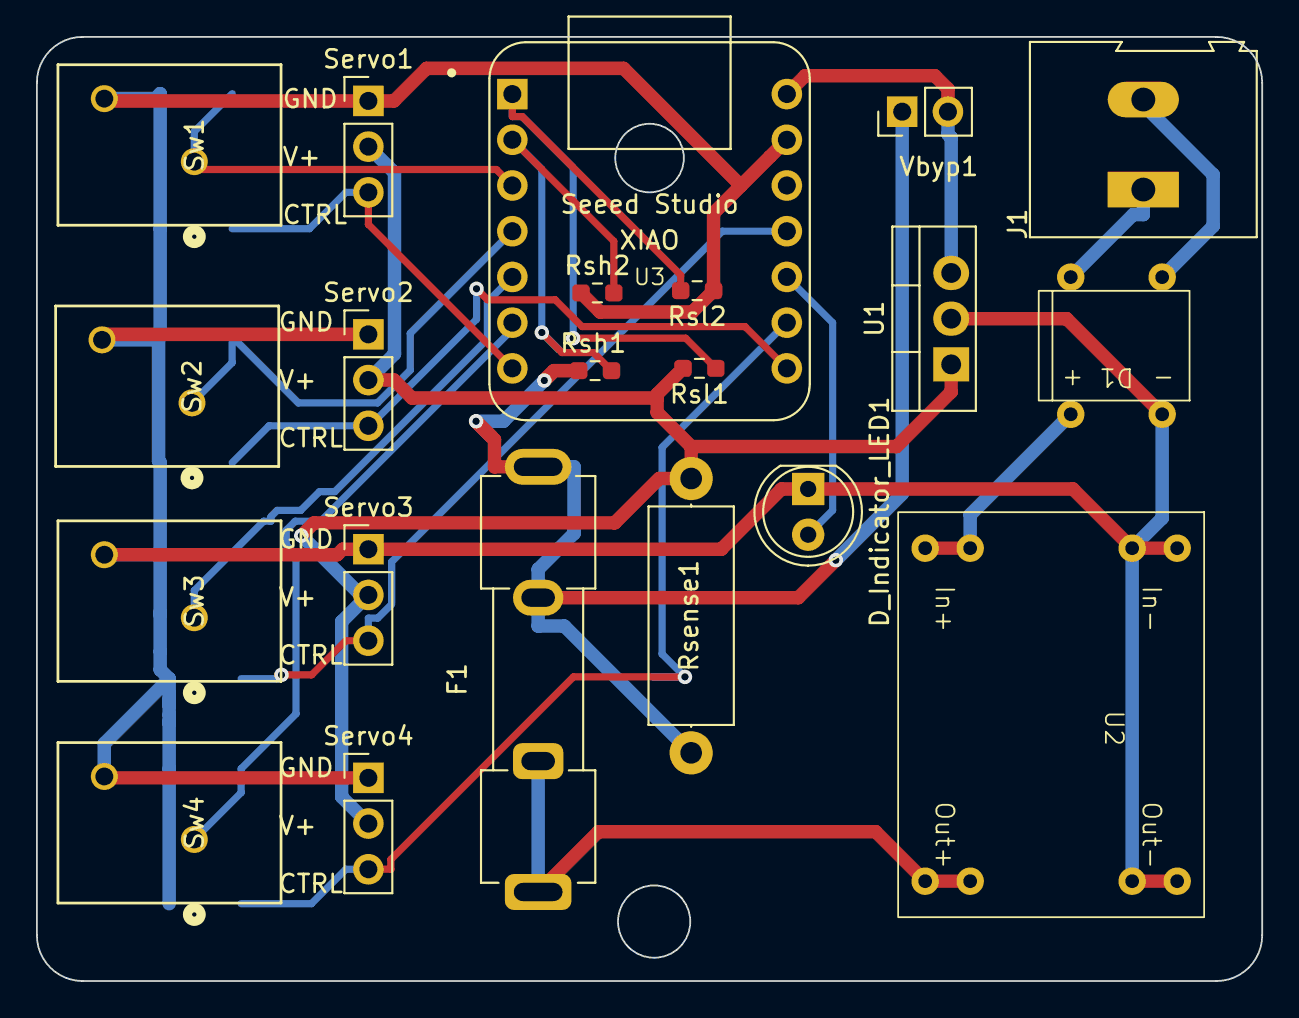
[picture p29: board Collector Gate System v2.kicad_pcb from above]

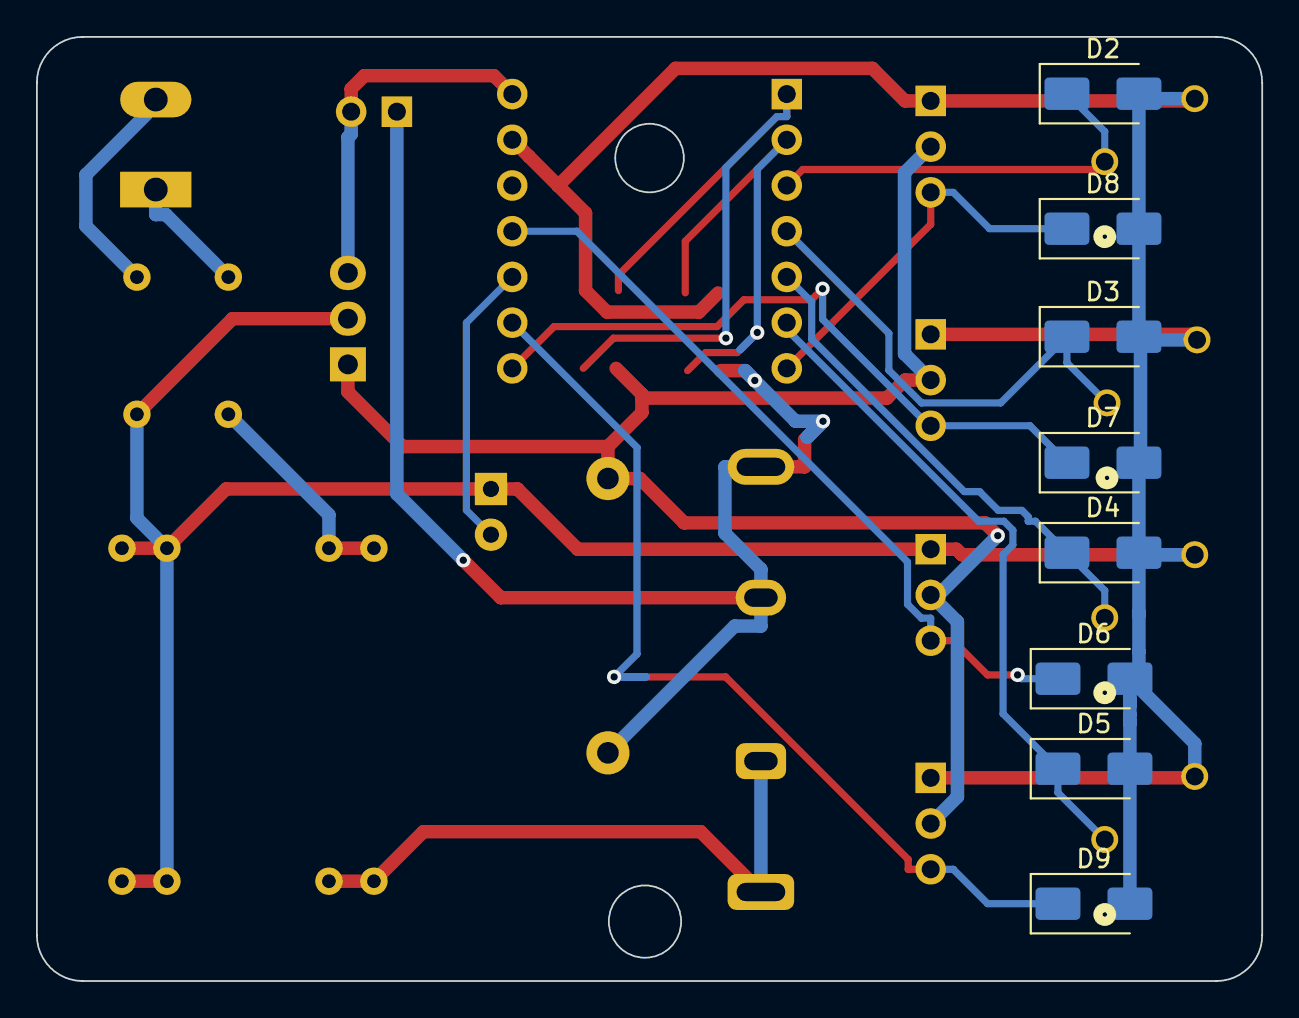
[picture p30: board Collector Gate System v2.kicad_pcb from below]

Board: 2 copper layers, 68.1 x 52.5 mm, 29 parts (8 on the bottom side), 19 nets.

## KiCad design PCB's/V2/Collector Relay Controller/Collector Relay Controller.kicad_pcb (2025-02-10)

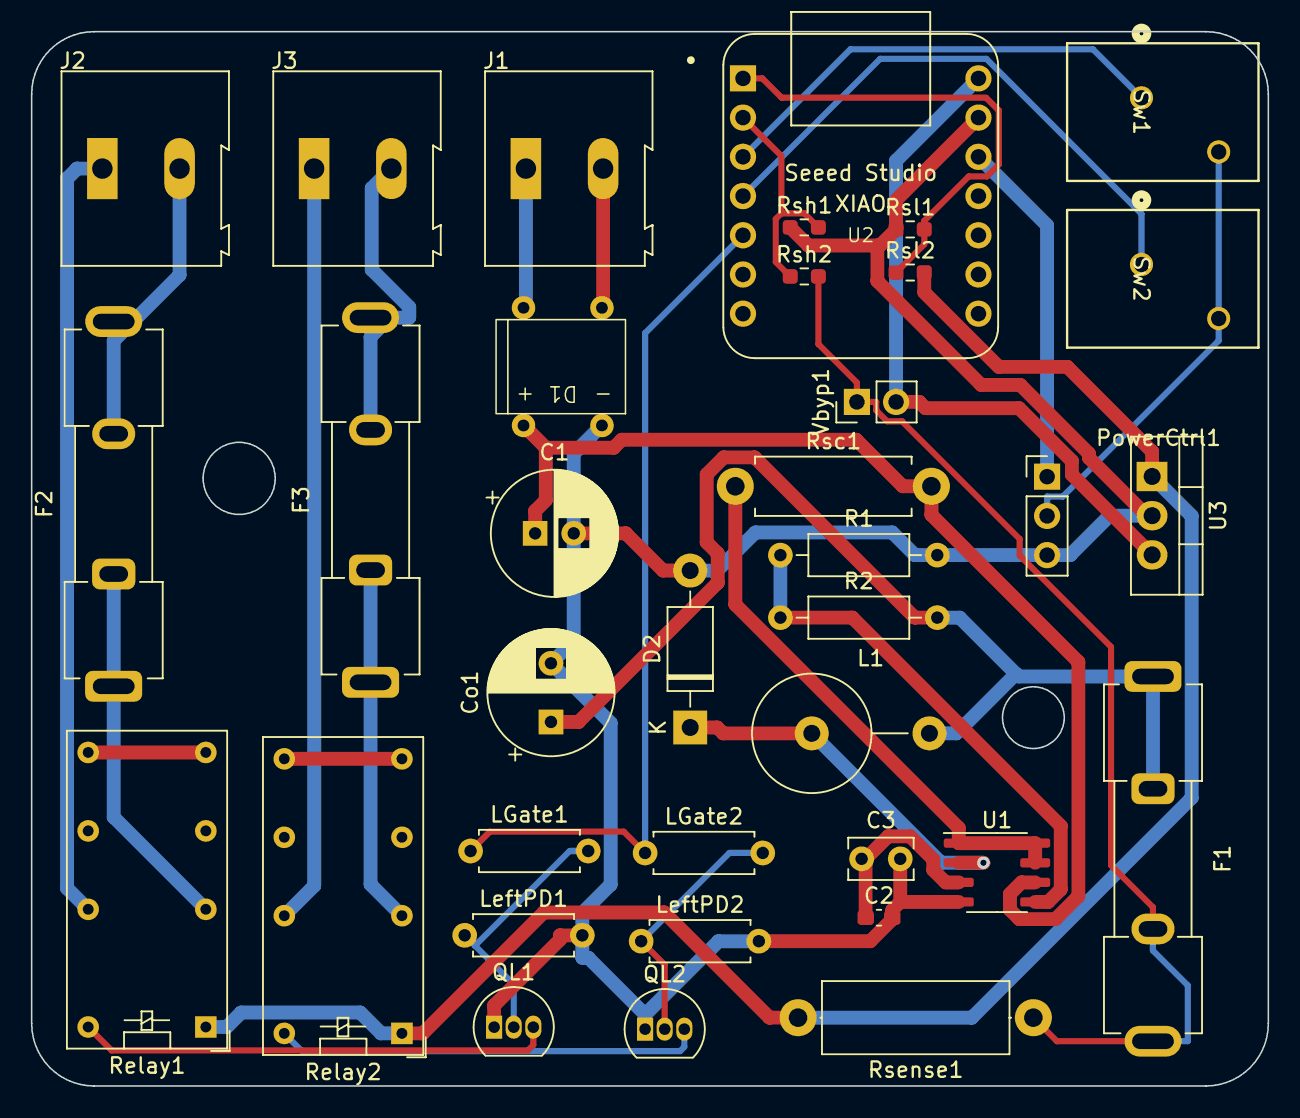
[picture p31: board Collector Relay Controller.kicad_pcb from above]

Board: 2 copper layers, 80.1 x 68.3 mm, 36 parts (0 on the bottom side), 31 nets.

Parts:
C1: C_Polarized; CP_Radial_D8.0mm_P2.50mm
C2: Ct; C_0603_1608Metric_Pad1.08x0.95mm_HandSolder
C3: Ct; C_Rect_L4.0mm_W2.5mm_P2.50mm
Co1: C_Polarized; CP_Radial_D8.0mm_P3.80mm
D1: D_Bridge_+-AA; DB_M
D2: 1N5819; D_DO-41_SOD81_P10.16mm_Horizontal
F1, F2, F3: Fuse_Small; Fuseholder_Clip-5x20mm_Keystone_3512P_Inline_P23.62x7.27mm_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
J1: 24Vac; TerminalBlock_Altech_AK300-2_P5.00mm
J2, J3: Contactor1; TerminalBlock_Altech_AK300-2_P5.00mm
L1: L; L_Axial_L16.0mm_D7.5mm_P7.62mm_Vertical_Fastron_XHBCC
LGate1, LGate2: R; R_Axial_DIN0207_L6.3mm_D2.5mm_P7.62mm_Horizontal
LeftPD1, LeftPD2: R; R_Axial_DIN0207_L6.3mm_D2.5mm_P7.62mm_Horizontal
PowerCtrl1: Conn_01x03_Pin; PinHeader_1x03_P2.54mm_Vertical
QL1, QL2: 2N7000; TO-92_Inline
R1, R2: R; R_Axial_DIN0207_L6.3mm_D2.5mm_P10.16mm_Horizontal
Relay1, Relay2: G5V-2; Relay_DPDT_Omron_G5V-2
Rsc1: R; R_Axial_DIN0411_L9.9mm_D3.6mm_P12.70mm_Horizontal
Rsense1: R; R_Axial_DIN0414_L11.9mm_D4.5mm_P15.24mm_Horizontal
Rsh1, Rsh2: R; R_0603_1608Metric_Pad0.98x0.95mm_HandSolder
Rsl1, Rsl2: R; R_0603_1608Metric_Pad0.98x0.95mm_HandSolder
Sw1, Sw2: Screw_Terminal_01x02; CONN_1985195
U1: MC33063AD; SOIC-8_3.9x4.9mm_P1.27mm
U2: XIAO-Generic-Thruhole-14P-2.54-21X17.8MM
U3: LM7805_TO220; TO-220-3_Vertical
Vbyp1: Conn_01x02_Pin; PinHeader_1x02_P2.54mm_Vertical

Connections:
/Control1: LGate1.1, LGate2.1, U2.5 (GPIO22)
/RsenseH: Rsh1.2, Rsh2.1, U2.2 (GPIO1)
/RsenseL: Rsl1.2, Rsl2.1, U2.1 (GPIO0)
/Switch Ctrl: PowerCtrl1.2, Sw1.2, Sw2.2
/Vboard: F1.2, Rsense1.1, Rsh2.2, Vbyp1.1
/Vout: Relay1.1, Relay2.1, Rsense1.2, Rsl2.2, U3.1 (VI)
GND: C1.2, C2.2, C3.2, Co1.2, D1.2 (-), D2.2 (A), LeftPD1.2, LeftPD2.2, PowerCtrl1.3, QL1.1 (S), QL2.1 (S), R1.2, Rsh1.1, Rsl1.1, U1.4 (GND), U2.13 (GND), U3.2 (GND)
unnamed: Co1.1, F1.1, L1.2, R2.2
unnamed: C1.1, D1.1 (+), Rsc1.2, U1.6 (Vin)
unnamed: D2.1 (K), L1.1, U1.2 (SwE)
unnamed: F2.1, Relay1.4
unnamed: F3.1, Relay2.4
unnamed: D1.4, J1.1
unnamed: D1.3, J1.2
unnamed: J2.1, Relay1.13
unnamed: F2.2, J2.2
unnamed: J3.1, Relay2.13
unnamed: F3.2, J3.2
unnamed: PowerCtrl1.1, U2.12 (3V3)
unnamed: QL1.3 (D), Relay1.16
unnamed: LGate1.2, LeftPD1.1, QL1.2 (G)
unnamed: QL2.3 (D), Relay2.16
unnamed: LGate2.2, LeftPD2.1, QL2.2 (G)
unnamed: Relay1.8, Relay1.9
unnamed: Relay2.8, Relay2.9
unnamed: Sw1.1, U2.3 (GPIO2)
unnamed: Sw2.1, U2.4 (GPIO21)
unnamed: Rsc1.1, U1.1 (SwC), U1.7 (Ipk), U1.8 (DC)
unnamed: C2.1, C3.1, U1.3 (TC)
unnamed: R1.1, R2.1, U1.5 (Vfb)
unnamed: U2.14 (5V), U3.3 (VO), Vbyp1.2

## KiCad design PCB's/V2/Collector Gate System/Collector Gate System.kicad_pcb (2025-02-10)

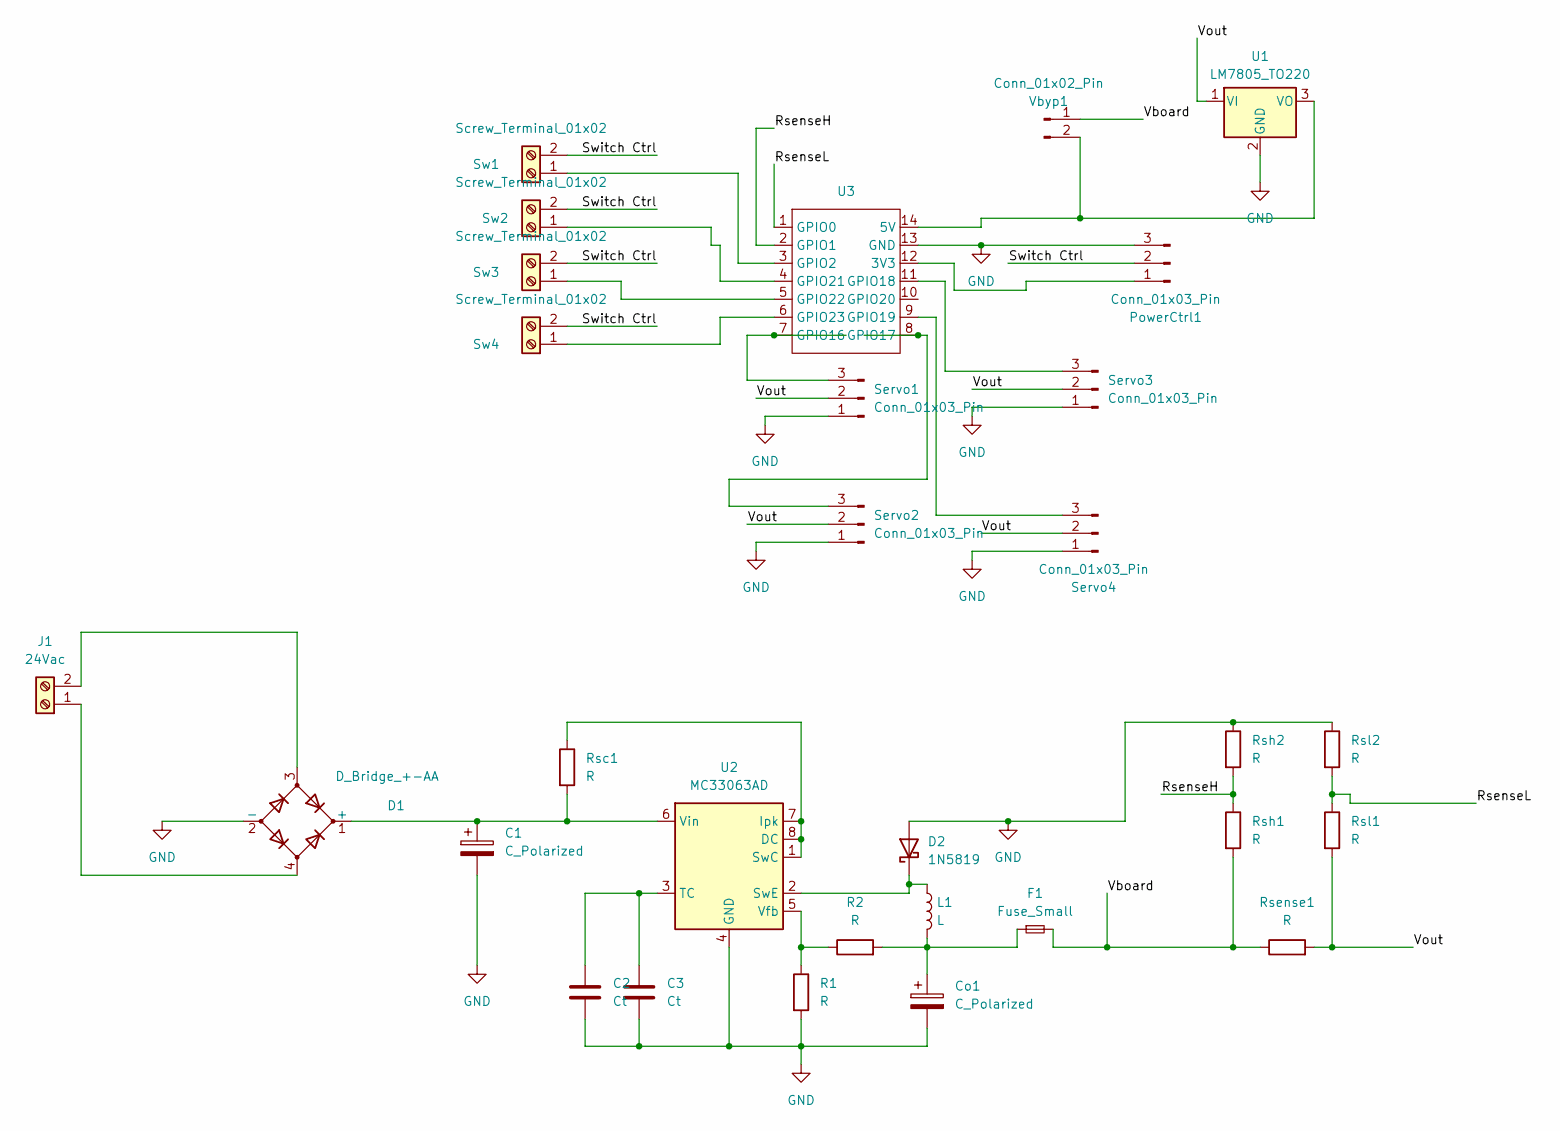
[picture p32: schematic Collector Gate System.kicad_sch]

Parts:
C1: C_Polarized; CP_Radial_D8.0mm_P2.50mm
C2: Ct; C_0603_1608Metric_Pad1.08x0.95mm_HandSolder
C3: Ct; C_Rect_L4.0mm_W2.5mm_P2.50mm
Co1: C_Polarized; CP_Radial_D8.0mm_P3.80mm
D1: D_Bridge_+-AA; DB_M
D2: 1N5819; D_DO-41_SOD81_P10.16mm_Horizontal
F1: Fuse_Small; Fuseholder_Clip-5x20mm_Keystone_3512P_Inline_P23.62x7.27mm_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
J1: 24Vac; TerminalBlock_Altech_AK300-2_P5.00mm
L1: L; L_Axial_L16.0mm_D7.5mm_P7.62mm_Vertical_Fastron_XHBCC
PowerCtrl1: Conn_01x03_Pin; PinHeader_1x03_P2.54mm_Vertical
R1, R2: R; R_Axial_DIN0207_L6.3mm_D2.5mm_P10.16mm_Horizontal
Rsc1: R; R_Axial_DIN0411_L9.9mm_D3.6mm_P12.70mm_Horizontal
Rsense1: R; R_Axial_DIN0414_L11.9mm_D4.5mm_P15.24mm_Horizontal
Rsh1, Rsh2: R; R_0603_1608Metric_Pad0.98x0.95mm_HandSolder
Rsl1, Rsl2: R; R_0603_1608Metric_Pad0.98x0.95mm_HandSolder
Servo1, Servo2, Servo3, Servo4: Conn_01x03_Pin; PinHeader_1x03_P2.54mm_Vertical
Sw1, Sw2, Sw3, Sw4: Screw_Terminal_01x02; CONN_1985195
U1: LM7805_TO220; TO-220-3_Vertical
U2: MC33063AD; SOIC-8_3.9x4.9mm_P1.27mm
U3: XIAO-Generic-Thruhole-14P-2.54-21X17.8MM
Vbyp1: Conn_01x02_Pin; PinHeader_1x02_P2.54mm_Vertical

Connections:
/RsenseH: Rsh1.1, Rsh2.2, U3.2 (GPIO1)
/RsenseL: Rsl1.1, Rsl2.2, U3.1 (GPIO0)
/Switch Ctrl: PowerCtrl1.2, Sw1.2, Sw2.2, Sw3.2, Sw4.2
/Vboard: F1.2, Rsense1.1, Rsh1.2, Vbyp1.1
/Vout: Rsense1.2, Rsl1.2, Servo1.2, Servo2.2, Servo3.2, Servo4.2, U1.1 (VI)
GND: C1.2, C2.2, C3.2, Co1.2, D1.2 (-), D2.2 (A), PowerCtrl1.3, R1.2, Rsh2.1, Rsl2.1, Servo1.1, Servo2.1, Servo3.1, Servo4.1, U1.2 (GND), U2.4 (GND), U3.13 (GND)
unnamed: Co1.1, F1.1, L1.2, R2.2
unnamed: C1.1, D1.1 (+), Rsc1.2, U2.6 (Vin)
unnamed: D2.1 (K), L1.1, U2.2 (SwE)
unnamed: D1.4, J1.1
unnamed: D1.3, J1.2
unnamed: PowerCtrl1.1, U3.12 (3V3)
unnamed: Servo1.3, U3.7 (GPIO16)
unnamed: Servo2.3, U3.8 (GPIO17)
unnamed: Servo3.3, U3.11 (GPIO18)
unnamed: Servo4.3, U3.9 (GPIO19)
unnamed: Sw1.1, U3.3 (GPIO2)
unnamed: Sw2.1, U3.4 (GPIO21)
unnamed: Sw3.1, U3.5 (GPIO22)
unnamed: Sw4.1, U3.6 (GPIO23)
unnamed: U1.3 (VO), U3.14 (5V), Vbyp1.2
unnamed: Rsc1.1, U2.1 (SwC), U2.7 (Ipk), U2.8 (DC)
unnamed: C2.1, C3.1, U2.3 (TC)
unnamed: R1.1, R2.1, U2.5 (Vfb)

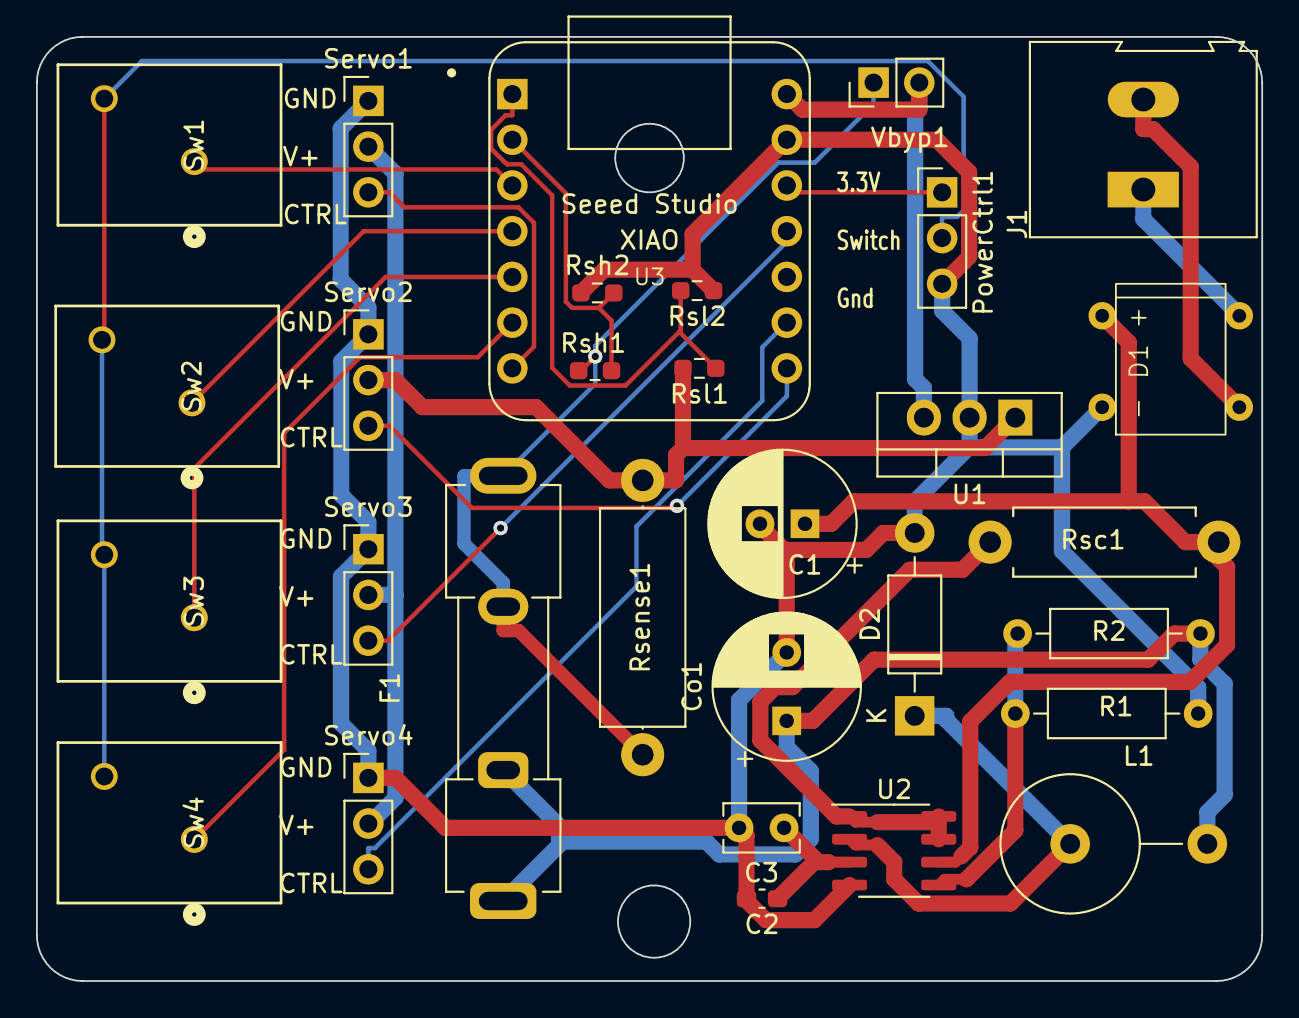
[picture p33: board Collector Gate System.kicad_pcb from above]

Board: 2 copper layers, 68.1 x 52.5 mm, 30 parts (0 on the bottom side), 24 nets.

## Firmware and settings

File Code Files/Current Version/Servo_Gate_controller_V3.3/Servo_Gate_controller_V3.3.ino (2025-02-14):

/* V3 has changed pinouts, and hopefully will add power monitoring controls to stop burning chipsets.
Uses dual ended current sensing now.
*/

#include <ESP32Servo.h>

#define BoardSel 2 //1 TS 2 Chop 3 BS
#define SenseEnable 0
#define loopdelay 30
#define loopstep 1
#define OpenGate 3
#define OpenBoard 1
#include <esp_now.h>
#include <WiFi.h>
const bool pull = 1; //0 for down 1 for up

#define NUM_BUTTONS 4
#define NUM_SERVOS 4
#define NUM_PEERS 5
#define NUM_BOARDS 3
#define waittime 1000
#define reboottime 5000

#define rebootpushenable 0
const int debounce[NUM_BOARDS] = {100,100,100};
const int buttonPins[NUM_BUTTONS] = {2, 21, 22, 23};  // Change as per your setup
//const int servoPins[NUM_SERVOS] = {23, 19, 20, 18};   
const int servoPins[NUM_SERVOS] = {16, 17, 18, 19};      // Change as per your setup
const int ActiveButtons[NUM_BOARDS] = {2,4,2};
//const int startlimit[NUM_SERVOS] = {0,0,0,0};  // Bandsaw, Spare Port
//const int endlimit[NUM_SERVOS]={150,160,60,60};
//const int startlimit[NUM_SERVOS] = {0,0,0,0}; // Planer, Chop L, Chop R, Router
//const int endlimit[NUM_SERVOS]={140,140,140,150};
//const int startlimit[NUM_SERVOS] = {0,0,0,0};  // Tablesaw,  side port
//const int endlimit[NUM_SERVOS]={145,150,60,60};

const int startlimits[NUM_BOARDS][NUM_SERVOS] = {
  {0,0,0,0},
  {0,0,0,0},
  {0,0,0,0}
  };  // Tablesaw,  side port
const int endlimits[NUM_BOARDS][NUM_SERVOS]={
{145,150,60,60}, // Table Saw

{140,140,140,150}, //Chop Saw

{150,160,60,60}, //Bandsaw


};

#define vss 5 // 6.1?
#define vcc 3.3
#define vratio 2
#define Rsense 0.47
#define calfac 0.5
#define ADCmax 3000.0
#define s_or_d 2
#define currentreadout 0
#define readthresh 0.5
#define readout2 1
#define currentThresh 1.5
const int powerPins[s_or_d] = {0,1};
float powerread[s_or_d];
float voltages[s_or_d];
float current;
bool currenttrigger;
const int* startlimit = startlimits[BoardSel-1];
const int* endlimit = endlimits[BoardSel-1];

unsigned long timer0[NUM_BUTTONS],timer1[NUM_BUTTONS];
unsigned long t2;
bool timerlock[NUM_BUTTONS];

int angle[NUM_SERVOS] = {0,0,0,0};
int pastangle[NUM_SERVOS] = {0,0,0,0};
bool gateflag = true;
bool quesend[NUM_BUTTONS];

int last_active = 10;

Servo servos[NUM_SERVOS]; 

typedef struct struct_message {
  bool CollectorState;
  bool ExtraState;
  int button;
  int board;
  bool reboot;
} struct_message;

struct_message myData;

const uint8_t broadcastAddresses[NUM_PEERS][6] = {
  {0xF0, 0xF5, 0xBD, 0x2C, 0xFF, 0x80}, // #3  Tablesaw Board
  {0xF0, 0xF5, 0xBD, 0x2D, 0x03, 0x58}, //#2   Chopsaw Board
  {0xF0, 0xF5, 0xBD, 0x2D, 0x14, 0x4C}, // #1  Bandsaw board

  {0xF0, 0xF5, 0xBD, 0x2C, 0xF9, 0xE0},  //DC V2
  {0x64, 0xE8, 0x33, 0x7F, 0x84, 0x3C},  //LED Monitor

//{0xDC, 0xDA, 0x0C, 0xCE, 0xF4, 0x8C},  //4 pin
  //{0x24, 0x6F, 0x28, 0xAE, 0xDC, 0x54}
};

void setup() {
  Serial.begin(115200);
  pinMode(LED_BUILTIN,OUTPUT);
  
  WiFi.mode(WIFI_STA);



  // Print the MAC address of the ESP32
  Serial.print("ESP32 MAC Address: ");
  Serial.println(WiFi.macAddress());
  Serial.print("Board Sel: ");
  Serial.println(BoardSel);
  Serial.print("Start Limits: ");
  for(int x = 0; x < 4; x++){
  Serial.print(startlimit[x]);
  Serial.print(" | ");}
  Serial.println();
  Serial.print("End Limits: ");
  for(int x = 0; x < 4; x++){
  Serial.print(endlimit[x]);
  Serial.print(" | ");}
  Serial.println();
  

  for (int i = 0; i < NUM_SERVOS; i++) {
    servos[i].attach(servoPins[i]);
    angle[i] = startlimit[i];
    pastangle[i] = angle[i];
    //if(OpenBoard == BoardSel){

    //if(i == OpenGate){
    //angle[i] = endlimit[i];
    //pastangle[i] = angle[i];  
  //}}
    servos[i].write(angle[i]);
    delay(1000);
  }


  for (int i = 0; i < NUM_SERVOS; i++) {
    servos[i].detach();}

  if (esp_now_init() != ESP_OK) {
    Serial.println("Error initializing ESP-NOW");
    return;
  }
  esp_now_register_send_cb(OnDataSent);
  esp_now_register_recv_cb(OnDataRecv);

  for (int i = 0; i < NUM_PEERS; i++) {
    if(i != BoardSel-1){
    esp_now_peer_info_t peerInfo;
    memcpy(peerInfo.peer_addr, broadcastAddresses[i], 6);
    peerInfo.channel = 0;  
    peerInfo.encrypt = false;
    if (esp_now_add_peer(&peerInfo) != ESP_OK) {
      Serial.println("Failed to add peer");
      return;
    }
  }}

  for (int i = 0; i < ActiveButtons[BoardSel-1]; i++) {
    if(pull == 0){
    pinMode(buttonPins[i], INPUT_PULLDOWN);}
    else{
      pinMode(buttonPins[i], INPUT_PULLUP);
    }
  }
Serial.println("Setup Complete");
}



void loop() {
  digitalWrite(LED_BUILTIN,LOW);
  readCurrent();
  for (int i = 0; i < NUM_BUTTONS; i++) {
      if (digitalRead(buttonPins[i]) == pull){  // reset timer flag
        timerlock[i] = false;
        timer0[i] = millis();
      }

    if (digitalRead(buttonPins[i]) == !pull) { // set the initial case
      if(timerlock[i] == false){
      timer0[i] = millis();
      timerlock[i] = true;
      }


      if(millis()-timer0[i] >= reboottime && rebootpushenable == 1){
        myData.reboot = true;
        for (int j = 0; j < NUM_PEERS; j++) {
          if(j != BoardSel-1){
        esp_now_send(broadcastAddresses[j], (uint8_t *) &myData, sizeof(myData));}
      }
      if(myData.reboot == true){
        Serial.println("Rebooting.......");        
        esp_restart();
      }

      }
    
      
      if(millis()-timer0[i] >= debounce[BoardSel-1]){
        quesend[i] = true;}}
        
        
      if(quesend[i] == true && digitalRead(buttonPins[i]) == pull){
        quesend[i] = false;       
        t2 = millis();
        Serial.print("Button: ");
        Serial.print(i+1);
        Serial.print("Pressed.  Timers: ");
        Serial.print(timer0[i]);
        Serial.print("  ");
        Serial.print(t2);
        timer1[i] = timer0[i];
        timer0[i] - millis();
        myData.button = i+1;
        myData.board = BoardSel;
        timerlock[i] = false;
             
      if(last_active == i){
        myData.CollectorState = !myData.CollectorState;
      }
      else{
        myData.CollectorState = 1;
      }
      last_active = i;

      lightLED(i);
      delay(waittime);  // Adjust delay as needed
      for (int j = 0; j < NUM_PEERS; j++) {
        if(j != BoardSel-1){
        esp_now_send(broadcastAddresses[j], (uint8_t *) &myData, sizeof(myData));}
      }

      turnOffAllLEDs(i);
      gateflag = false;
      }
    
  

for(int j = 0; j < NUM_SERVOS; j++){
        
        
        if(pastangle[j] < angle[j]){
          servos[j].attach(servoPins[j]);
          Serial.print("Gate ");
          Serial.print(j+1);
          Serial.println(" Opening");
          gateflag = true;
          for(int i = pastangle[j]; i <= angle[j]; i++){
            readCurrent();
            //Serial.println(i);
            servos[j].write(i);
            delay(loopdelay);
          }
          servos[j].detach();
          pastangle[j] = angle[j];}
          
                  
        if(pastangle[j] > angle[j] && gateflag == true){
          servos[j].attach(servoPins[j]);
          Serial.print("Gate ");
          Serial.print(j+1);
          Serial.println(" Closing");
          for(int i = pastangle[j]; i >= angle[j]; i--){
            readCurrent();
            //Serial.println(i);
            servos[j].write(i);
            delay(loopdelay);

          }
          servos[j].detach();
          pastangle[j] = angle[j];}
}

}
}

void readCurrent(){
for (int i = 0; i < s_or_d; i++){
powerread[i] = analogRead(powerPins[i]);
voltages[i] = vcc/ADCmax*powerread[i]*vratio;
if(currentreadout == 1 || current >= readthresh){
Serial.print("V");
Serial.print(i+1);
Serial.print(" ");
Serial.print(voltages[i]);
Serial.print(" | ");}

}
current = calfac*abs(voltages[1]-voltages[0])/Rsense;

if(current >= readthresh){
  
Serial.print(" Current ");
Serial.println(current);}
if(currentreadout == 1){
Serial.print(" Current ");
Serial.println(current);}
if(current > currentThresh && currenttrigger == false && SenseEnable == 1){
  if(readout2 == 1){
  Serial.print("Current: ");
  Serial.print(current);
  Serial.println("Current Trigger");}
  currenttrigger = true;
  esp_restart();
}
}


void lightLED(int index) {
  angle[index] = endlimit[index];
  Serial.print(index);
  Serial.println(servoPins[index]);

  //digitalWrite(ledPins[index], HIGH);
}

void turnOffAllLEDs(int index) {
  for (int i = 0; i < NUM_SERVOS; i++) {
    if(i != index){
      angle[i] = startlimit[i];

      //digitalWrite(ledPins[i], LOW);
      }
  }
}

void OnDataSent(const uint8_t *mac_addr, esp_now_send_status_t status) {
  delay(50);
  Serial.print("Last Packet Send Status: ");
  Serial.println(status == ESP_NOW_SEND_SUCCESS ? "Delivery Success" : "Delivery Fail");
}

void OnDataRecv(const esp_now_recv_info* recv_info, const uint8_t* incomingData, int len) {
  memcpy(&myData, incomingData, sizeof(myData));
  if(myData.reboot == true){
    Serial.println("Received reboot command");
    esp_restart();
  }

  last_active = 10;
  Serial.print("DC State");
  Serial.println(myData.CollectorState);
  Serial.print("Board: ");
  Serial.print(myData.board);
  Serial.print(" Button: ");
  Serial.println(myData.button);
  
  if(myData.board != 0){
  delay(waittime);  // Adjust delay as needed
  turnOffAllLEDs(5);}
  else{
    Serial.println("Dust Remote Triggered");
  }
}

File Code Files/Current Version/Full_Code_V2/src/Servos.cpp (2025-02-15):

#include "Servos.h"
#include "Current_Sense.h"
#include "Settings.h"
#include "mesh_network.h"
// Define the gateflag variable
bool gateflag = true;

// Ensure extern variables are declared
const int debounce[NUM_GATE_BOARDS] = {100, 100, 100}; // Updated constant name
const int buttonPins[NUM_BUTTONS] = {2, 21, 22, 23};  // Change as per your setup
const int servoPins[NUM_SERVOS] = {16, 17, 18, 19};   // Change as per your setup
const int ActiveButtons[NUM_GATE_BOARDS] = {2, 4, 2}; // Updated constant name

const int startlimits[NUM_GATE_BOARDS][NUM_SERVOS] = { // Updated constant name
    {0, 0, 0, 0},
    {0, 0, 0, 0},
    {0, 0, 0, 0}};
const int endlimits[NUM_GATE_BOARDS][NUM_SERVOS] = { // Updated constant name
    {145, 150, 60, 60},  // Table Saw
    {140, 140, 140, 150}, // Chop Saw
    {150, 160, 60, 60},  // Bandsaw
};

const int *startlimit = startlimits[BoardSel];
const int *endlimit = endlimits[BoardSel];

Servo servos[NUM_SERVOS];
int angle[NUM_SERVOS];
int pastangle[NUM_SERVOS];

void Initialize_Servos() {
    for (int i = 0; i < NUM_SERVOS; i++) {
        servos[i].attach(servoPins[i]);
        angle[i] = startlimit[i];
        pastangle[i] = angle[i];
        servos[i].write(angle[i]);
        delay(1000);
    }

    //for (int i = 0; i < NUM_SERVOS; i++) {
      //  servos[i].detach();}
    
}

void write_servo_position() {
    static bool newdata = false;
    static bool targetreached = false;
    for(int k = 0; k < NUM_SERVOS; k++){   
        if(angle[k] != pastangle[k]){
            newdata=true;
        }}
        if(newdata==true){
            //PrintCommandedAngles();
            //PrintLocalGateArrays();
            newdata = false;
        }
        

    for (int j = 0; j < NUM_SERVOS; j++) {
        if (pastangle[j] < angle[j]) {
            //servos[j].attach(servoPins[j]);
            Serial.print("Gate ");
            Serial.print(GateNames[BoardSel][j]);
            Serial.println(" Opening");
            gateflag = true;
            for (int i = pastangle[j]; i <= angle[j]; i++) {
                readCurrent();
                // Serial.println(i);
                servos[j].write(i);
                delay(loopdelay);
            }
            //servos[j].detach();
            pastangle[j] = angle[j];
        }

        if (pastangle[j] > angle[j] && gateflag == true) {
            //servos[j].attach(servoPins[j]);
            Serial.print("Gate ");
            Serial.print(GateNames[BoardSel][j]);
            Serial.println(" Closing");
            for (int i = pastangle[j]; i >= angle[j]; i--) {
                readCurrent();
                // Serial.println(i);
                servos[j].write(i);
                delay(loopdelay);
            }
            //servos[j].detach();
            pastangle[j] = angle[j];
        }
    }
}

void updateServoAngles(bool shortPress[], bool longPress[]) {
    for (int i = 0; i < NUM_SERVOS; i++) {
        if (shortPress[i] || longPress[i]) {
            angle[i] = endlimit[i];
        } else {
            angle[i] = startlimit[i];
        }
    }
}

void PrintCommandedAngles(){
    Serial.print("Commanded Angles | (");
    for(int i = 0; i < NUM_SERVOS; i++){
        Serial.print(angle[i]);
        Serial.print(", ");
    }
    Serial.println(")");
}

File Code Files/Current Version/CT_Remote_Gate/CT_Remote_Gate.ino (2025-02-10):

#include <WiFi.h>
#include <esp_now.h>

#define NUM_RELAYS 9
#define WAKE_THRESHOLD 200000 // Adjust threshold as needed
#define SLEEP_MIN 1
#define LED_PIN 3
#define PWR_LED 43
#define WAKEUP_BUTTON_PIN 2 // GPIO pin for the wake-up button
#define FLASHTIME 200
#define FLASHCOUNT 5
#define NUM_PEERS 4

typedef struct struct_message {
  bool CollectorState;
  bool ExtraState;
  int button;
  int board = 0;
  bool reboot;
} struct_message;

struct_message myData;

const uint8_t broadcastAddresses[NUM_PEERS][6] = {
  {0xF0, 0xF5, 0xBD, 0x2D, 0x14, 0x4C}, // #1  Bandsaw board
  {0xF0, 0xF5, 0xBD, 0x2C, 0xF4, 0x8C}, // #2  Chopsaw Board
  {0xF0, 0xF5, 0xBD, 0x2C, 0xFA, 0xC8}, // #3  Tablesaw Board
  {0xF0, 0xF5, 0xBD, 0x2C, 0xF9, 0xE0}, // DC V2
  // Unused addresses commented out
};

bool relayStates[NUM_RELAYS] = {false};
bool lastSentSuccess = true;
bool ContactorState = false;
unsigned long startTime;
const unsigned long SLEEP_TIME = SLEEP_MIN * 60 * 1000;
bool anyRelayOn = false;

void setup() {
  Serial.begin(115200);
  WiFi.mode(WIFI_STA);
  delay(20); // Give some time for the serial monitor to connect
  Serial.print("MAC Address: ");
  Serial.println(WiFi.macAddress());
  Serial.println("Starting setup...");

  pinMode(LED_PIN, OUTPUT);
  digitalWrite(LED_PIN, 1);
  pinMode(PWR_LED, OUTPUT);
  digitalWrite(PWR_LED, HIGH);

  // Configure push button pin for wake-up
  pinMode(WAKEUP_BUTTON_PIN, INPUT_PULLDOWN);
  esp_sleep_enable_ext0_wakeup((gpio_num_t)WAKEUP_BUTTON_PIN, HIGH);

  if (esp_now_init() != ESP_OK) {
    Serial.println("Error initializing ESP-NOW");
    return;
  }
  Serial.println("ESP-NOW initialized");

  esp_now_register_send_cb(OnDataSent);

  for (int i = 0; i < NUM_PEERS; i++) {
    esp_now_peer_info_t peerInfo;
    memset(&peerInfo, 0, sizeof(peerInfo)); // Initialize the struct
    memcpy(peerInfo.peer_addr, broadcastAddresses[i], 6);
    peerInfo.channel = 0;
    peerInfo.encrypt = false;
    if (esp_now_add_peer(&peerInfo) != ESP_OK) {
      Serial.println("Failed to add peer");
      return;
    }
  }
  
  startTime = millis();
  Serial.println("Setup complete");
}

void loop() {
  if (digitalRead(WAKEUP_BUTTON_PIN) == HIGH) {
    delay(50); // Debounce delay
    while (digitalRead(WAKEUP_BUTTON_PIN) == HIGH); // Wait for button release
    delay(50);
    Serial.println("Wake-up button activated");
    // Toggle relay state
    myData.CollectorState = ! myData.CollectorState;

    for (int j = 0; j < NUM_PEERS; j++) {
      esp_now_send(broadcastAddresses[j], (uint8_t *) &myData, sizeof(myData));
      startTime = millis(); // Reset the start time
    }
  }

  if (millis() - startTime >= SLEEP_TIME) {
    Serial.println("Entering deep sleep...");
    enterDeepSleep();
  }

  if(myData.CollectorState == false){
    analogWrite(LED_PIN,20);
  } else {
    analogWrite(LED_PIN,255);
  }
}

void enterDeepSleep() {
  Serial.println("Preparing to sleep...");
  // Optional: Disable WiFi to save more power before sleep
  WiFi.disconnect(true);
  delay(100); // Give time for WiFi to disconnect properly
  esp_deep_sleep_start();
}

void OnDataSent(const uint8_t *mac_addr, esp_now_send_status_t status) {
  Serial.print("Last Packet Send Status: ");
  Serial.println(status == ESP_NOW_SEND_SUCCESS ? "Delivery Success" : "Delivery Fail");
}

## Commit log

2025-02-10 Code Files and Readme
    [6 inch gate pinion.stl, 6 inch gate rack.stl, 6 inch gate servo holder.stl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]
2025-02-15 Ready except current sensing controls
2025-02-15 Looks to be complete e xcept power monitoring
2025-02-15 LEDs dont play with Wifi, Timers enabled
2025-08-09 re-enabled current sensing added LED
2025-08-13 re-enabled current sense, added Vref LED
2025-09-14 V3 Live
    [4 inch servo gate geared v11.3mf, 6 Inch servo gate v3.3mf]
